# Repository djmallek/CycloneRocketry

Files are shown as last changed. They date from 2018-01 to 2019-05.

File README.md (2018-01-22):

# Cyclone Rocketry

This is an avionics control board for Iowa State's Cyclone Rocketry club. Our rocketry must carry a payload to a target altitude of 10,000ft.  Score is determined by how close a team's rocket can get to the target altitude, among other things.  To ensure we hit our target altitude, we have an air brakes system which actively calculates when and how long it needs to deploy it's air brakes system.  The board additionally provides data-logging and radio-relayed GPS tracking.

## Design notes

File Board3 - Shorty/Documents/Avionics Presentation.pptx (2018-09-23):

## Avionics Board

Danny

## What it do?

- Take environmental data (sensors)
- Log data
- Calculate when to move airbrakes
- Move airbrakes

## Sensors?

- IMU (gyro + accelerometer)
- Barometer (pressure sensor)
- Temperature
- GPS (location + super accurate time)
- Airbrake Position

## What else?

- 900MHz Radio for transmitting location
- Micro SD Card for datalogging
- Position monitoring of airbrakes
- Control of airbrakes using PWM (Pulse width modulation)
- Battery charging circuit (charges over USB)

## How to program?

- Through Arduino IDE! Super Easy!
- Go here: https://learn.adafruit.com/adafruit-feather-m0-basic-proto/setup and follow the instructions for “Arduino IDE Setup”, “Using with Arduino IDE”, and “Adapting Sketches to M0”

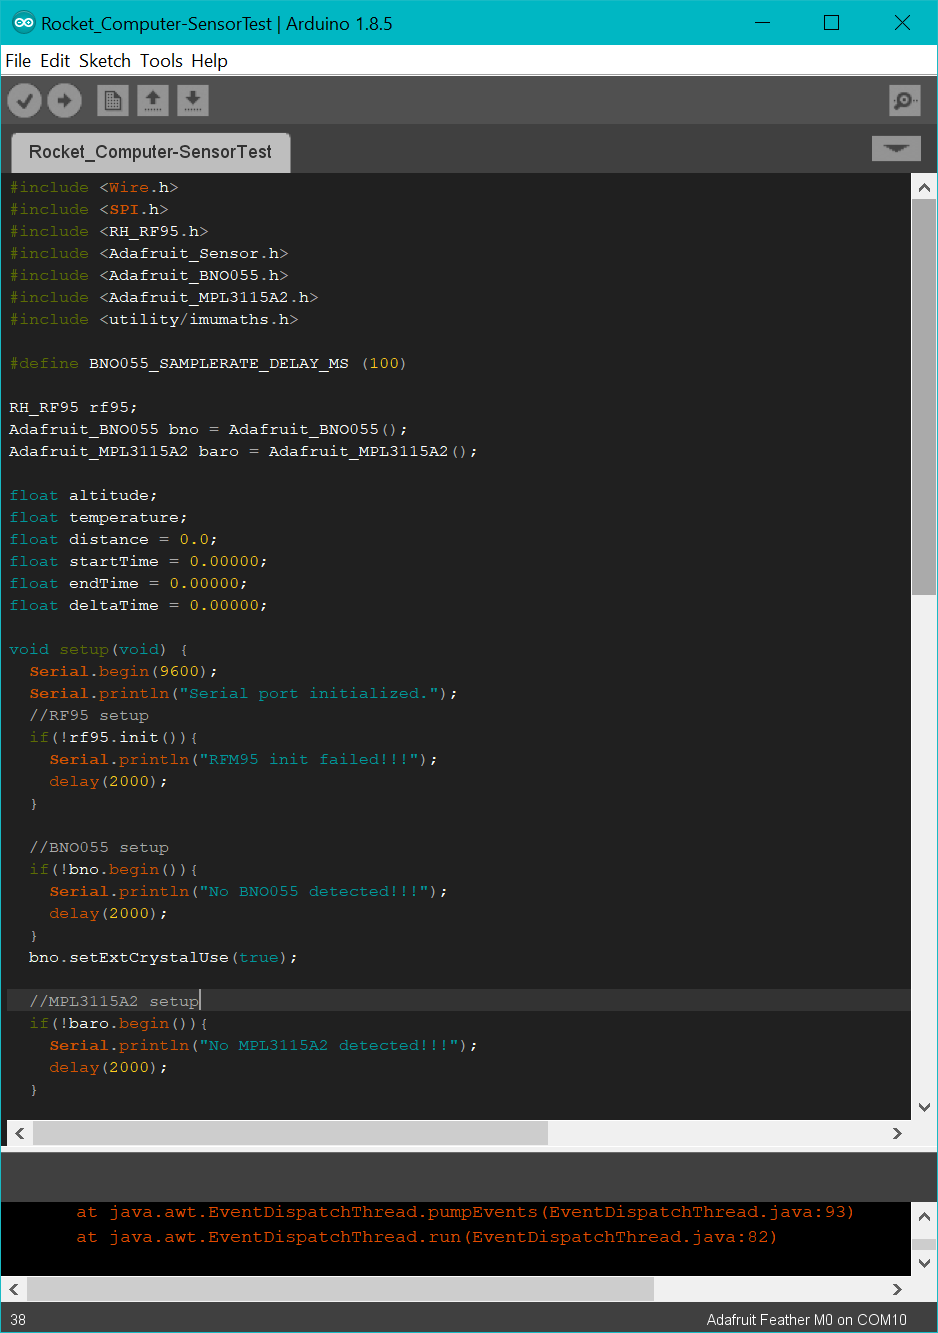
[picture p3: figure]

## Pictures

Manifest logo will change to Rocket Shop

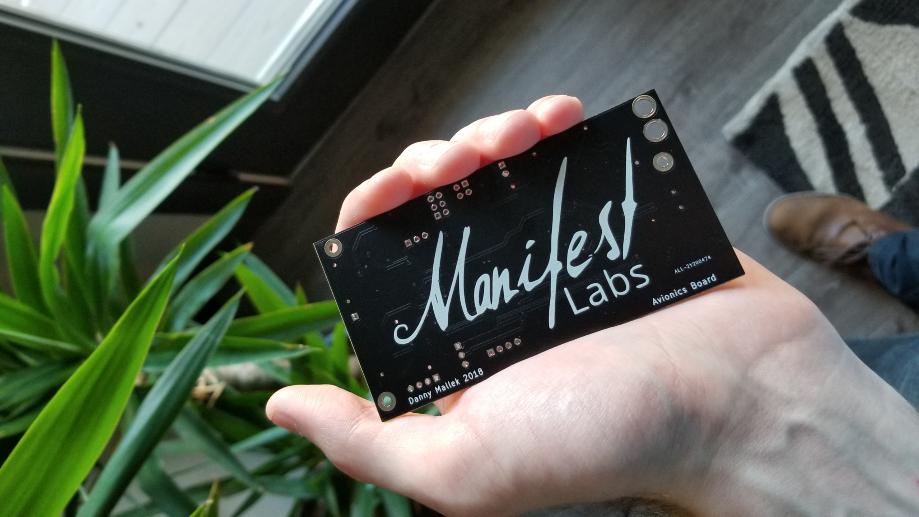
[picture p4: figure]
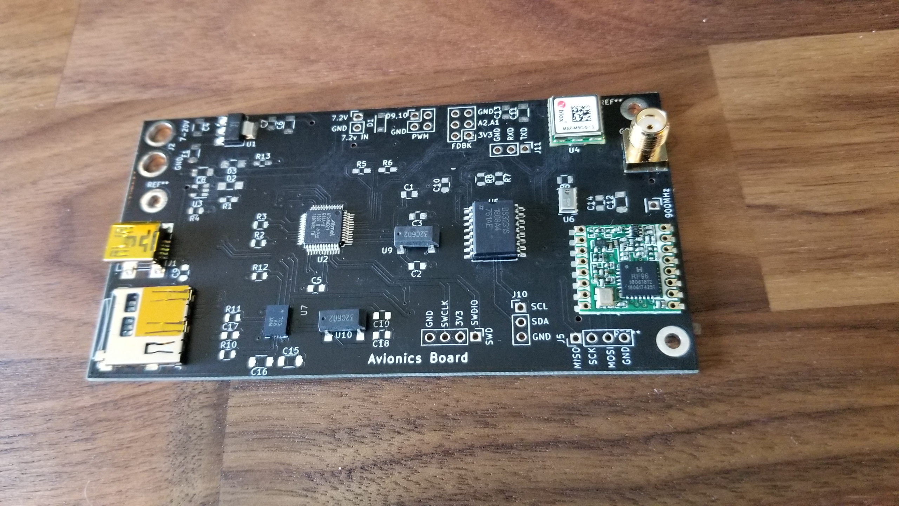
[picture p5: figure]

## Looking forward

- Avionics Board
  - Add status LEDs
  - Better power systems
  - Smaller board
  - Better connectors
  - More sensors? A second accelerometer for higher G’s?

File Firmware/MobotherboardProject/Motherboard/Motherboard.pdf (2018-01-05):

## Motherboard Project Configuration Report

# 1. Description

## 1.1. Project

Project Name | Motherboard
Board Name | Motherboard
Generated with: | STM32CubeMX 4.20.1
Date | 06/13/2017

## 1.2. MCU

MCU Series | STM32F4
MCU Line | STM32F411
MCU name | STM32F411RETx
MCU Package | LQFP64
MCU Pin number | 64

# 2. Pinout Configuration

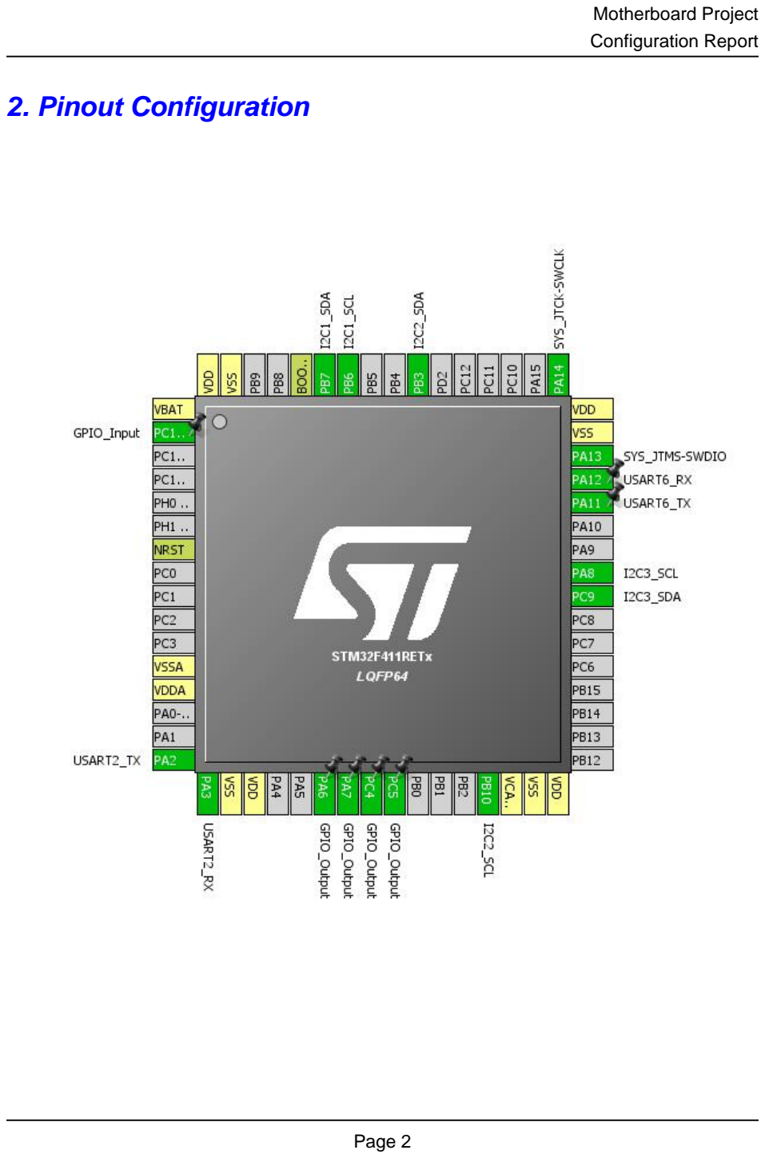
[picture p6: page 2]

# 3. Pins Configuration

Pin Number LQFP64 | Pin Name (function after reset) | Pin Type | Alternate Function(s) | Label
1 | VBAT | Power
2 | PC13-ANTI_TAMP * | I/O | GPIO_Input
7 | NRST | Reset
12 | VSSA | Power
13 | VDDA | Power
16 | PA2 | I/O | USART2_TX
17 | PA3 | I/O | USART2_RX
18 | VSS | Power
19 | VDD | Power
22 | PA6 * | I/O | GPIO_Output
23 | PA7 * | I/O | GPIO_Output
24 | PC4 * | I/O | GPIO_Output
25 | PC5 * | I/O | GPIO_Output
29 | PB10 | I/O | I2C2_SCL
30 | VCAP1 | Power
31 | VSS | Power
32 | VDD | Power
40 | PC9 | I/O | I2C3_SDA
41 | PA8 | I/O | I2C3_SCL
44 | PA11 | I/O | USART6_TX
45 | PA12 | I/O | USART6_RX
46 | PA13 | I/O | SYS_JTMS-SWDIO
47 | VSS | Power
48 | VDD | Power
49 | PA14 | I/O | SYS_JTCK-SWCLK
55 | PB3 | I/O | I2C2_SDA
58 | PB6 | I/O | I2C1_SCL
59 | PB7 | I/O | I2C1_SDA
60 | BOOT0 | Boot
63 | VSS | Power
64 | VDD | Power

## * The pin is affected with an I/O function

# 4. Clock Tree Configuration

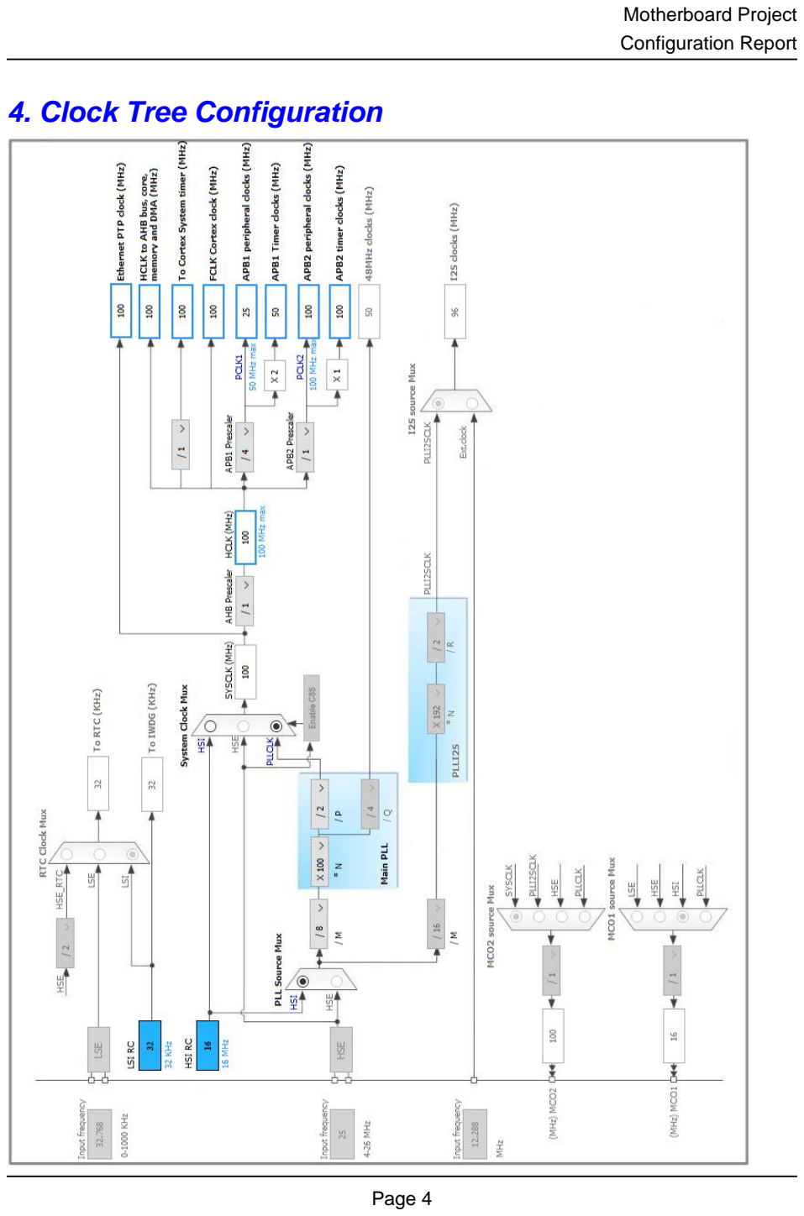
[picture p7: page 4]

# 5. IPs and Middleware Configuration

# 5.1. I2C1

## I2C: I2C

## 5.1.1. Parameter Settings:

### Master Features:

I2C Speed Mode | Standard Mode
I2C Clock Speed (Hz) | 100000

### Slave Features:

Clock No Stretch Mode | Disabled
Primary Address Length selection | 7-bit
Dual Address Acknowledged | Disabled
Primary slave address | 0
General Call address detection | Disabled

# 5.2. I2C2

## I2C: I2C

## 5.2.1. Parameter Settings:

### Master Features:

I2C Speed Mode | Standard Mode
I2C Clock Speed (Hz) | 100000

### Slave Features:

Clock No Stretch Mode | Disabled
Primary Address Length selection | 7-bit
Dual Address Acknowledged | Disabled
Primary slave address | 0
General Call address detection | Disabled

# 5.3. I2C3

## I2C: I2C

## 5.3.1. Parameter Settings:

### Master Features:

I2C Speed Mode | Standard Mode
I2C Clock Speed (Hz) | 100000

### Slave Features:

Clock No Stretch Mode | Disabled
Primary Address Length selection | 7-bit
Dual Address Acknowledged | Disabled
Primary slave address | 0
General Call address detection | Disabled

# 5.4. SYS

## Debug: Serial Wire Timebase Source: SysTick

# 5.5. USART2

## Mode: Asynchronous

## 5.5.1. Parameter Settings:

### Basic Parameters:

Baud Rate | 9600 *
Word Length | 8 Bits (including Parity)
Parity | None
Stop Bits | 1

### Advanced Parameters:

Data Direction | Receive and Transmit
Over Sampling | 16 Samples

# 5.6. USART6

## Mode: Asynchronous

## 5.6.1. Parameter Settings:

### Basic Parameters:

Baud Rate | 9600 *
Word Length | 8 Bits (including Parity)
Parity | None
Stop Bits | 1

### Advanced Parameters:

Data Direction | Receive and Transmit
Over Sampling | 16 Samples

### * User modified value

# 6. System Configuration

# 6.1. GPIO configuration

IP | Pin | Signal | GPIO mode | GPIO pull/up pull down | Max Speed | User Label
I2C1 | PB6 | I2C1_SCL | Alternate Function Open Drain | Pull-up | Very High *
| PB7 | I2C1_SDA | Alternate Function Open Drain | Pull-up | Very High *
I2C2 | PB10 | I2C2_SCL | Alternate Function Open Drain | Pull-up | Very High *
| PB3 | I2C2_SDA | Alternate Function Open Drain | Pull-up | Very High *
I2C3 | PC9 | I2C3_SDA | Alternate Function Open Drain | Pull-up | Very High *
| PA8 | I2C3_SCL | Alternate Function Open Drain | Pull-up | Very High *
SYS | PA13 | SYS_JTMS-SWDIO | n/a | n/a | n/a
| PA14 | SYS_JTCK-SWCLK | n/a | n/a | n/a
USART2 | PA2 | USART2_TX | Alternate Function Push Pull | Pull-up | Very High *
| PA3 | USART2_RX | Alternate Function Push Pull | Pull-up | Very High *
USART6 | PA11 | USART6_TX | Alternate Function Push Pull | Pull-up | Very High *
| PA12 | USART6_RX | Alternate Function Push Pull | Pull-up | Very High *
GPIO | PC13-ANTI_TAMP | GPIO_Input | Input mode | Pull-down * | n/a
| PA6 | GPIO_Output | Output Push Pull | No pull-up and no pull-down | Low
| PA7 | GPIO_Output | Output Push Pull | No pull-up and no pull-down | Low
| PC4 | GPIO_Output | Output Push Pull | No pull-up and no pull-down | Low
| PC5 | GPIO_Output | Output Push Pull | No pull-up and no pull-down | Low

# 6.2. DMA configuration

## nothing configured in DMA service

# 6.3. NVIC configuration

Interrupt Table | Enable | Preenmption Priority | SubPriority
Non maskable interrupt | true | 0 | 0
Hard fault interrupt | true | 0 | 0
Memory management fault | true | 0 | 0
Pre-fetch fault, memory access fault | true | 0 | 0
Undefined instruction or illegal state | true | 0 | 0
System service call via SWI instruction | true | 0 | 0
Debug monitor | true | 0 | 0
Pendable request for system service | true | 0 | 0
System tick timer | true | 0 | 0
PVD interrupt through EXTI line 16 | unused
Flash global interrupt | unused
RCC global interrupt | unused
I2C1 event interrupt | unused
I2C1 error interrupt | unused
I2C2 event interrupt | unused
I2C2 error interrupt | unused
USART2 global interrupt | unused
USART6 global interrupt | unused
I2C3 event interrupt | unused
I2C3 error interrupt | unused
FPU global interrupt | unused

### * User modified value

# 7. Power Consumption Calculator report

### 7.1. Microcontroller Selection

Series | STM32F4
Line | STM32F411
MCU | STM32F411RETx
Datasheet | 026289_Rev4

### 7.2. Parameter Selection

Temperature | 25
Vdd | null

# 8. Software Project

## 8.1. Project Settings

Name | Value
Project Name | Motherboard
Project Folder | C:\Users\djmal\Documents\GitHub\FoxWestern\Firmware\MobotherboardProject\
Toolchain / IDE | SW4STM32
Firmware Package Name and Version | STM32Cube FW_F4 V1.16.0

## 8.2. Code Generation Settings

Name | Value
STM32Cube Firmware Library Package | Copy only the necessary library files
Generate peripheral initialization as a pair of '.c/.h' files | No
Backup previously generated files when re-generating | No
Delete previously generated files when not re-generated | Yes
Set all free pins as analog (to optimize the power consumption) | No

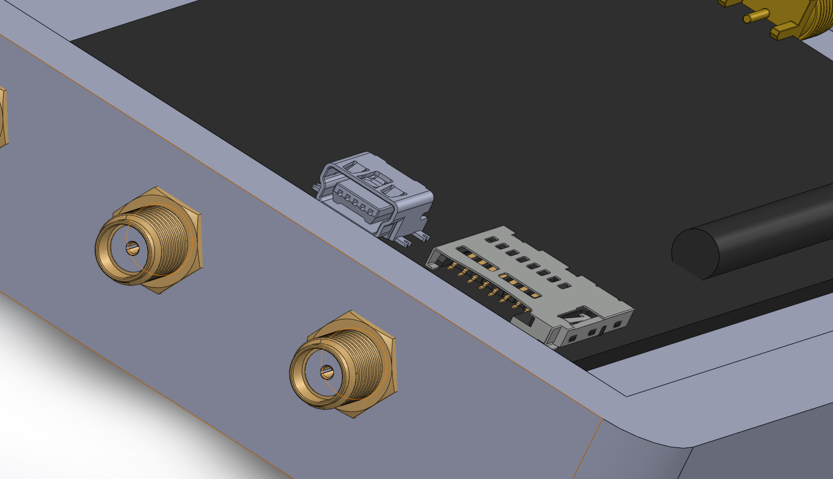
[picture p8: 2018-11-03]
Board3 - Shorty/Documents/Avionics Chassis/Screenshots/shot6.PNG

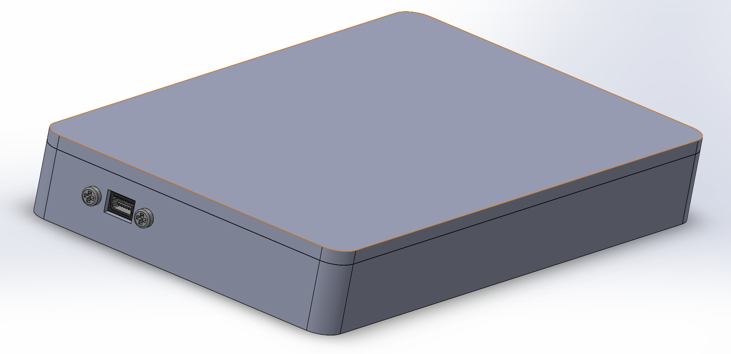
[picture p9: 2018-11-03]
Board3 - Shorty/Documents/Avionics Chassis/Screenshots/shot1.PNG

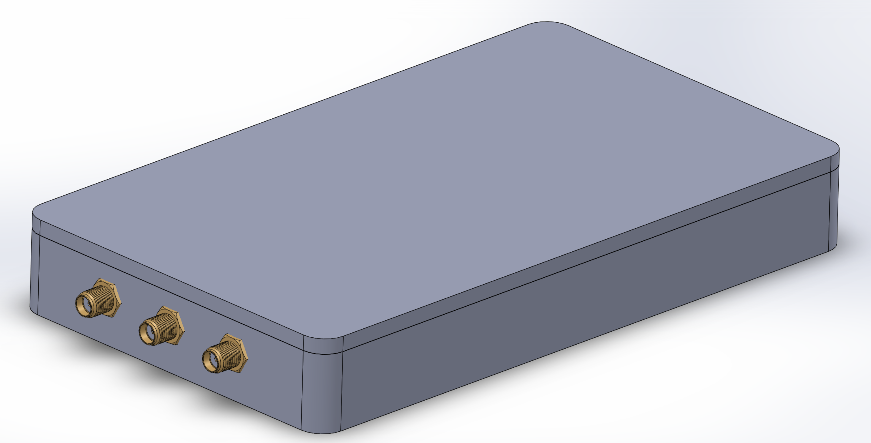
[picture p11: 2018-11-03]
Board3 - Shorty/Documents/Avionics Chassis/Screenshots/shot2.PNG

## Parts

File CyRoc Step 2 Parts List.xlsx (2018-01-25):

Part Name | Vendor | Part Number | Price Each | Qty | Total Price | Description
2.54mm Male Header (https://www.amazon.com/Hotop-Pack-Single-Header-Connector/dp/B06XR8CV8P) | Amazon | B06XR8CV8P | $6.99 | 1 | $6.99
2.54mm Female Header (https://www.amazon.com/2-54mm-Straight-Single-Female-Headers/dp/B00899WQ6U) | Amazon | B00899WQ6U | $4.63 | 1 | $4.63
Female XT60 (https://www.amazon.com/Finware-Female-Bullet-Connectors-Battery/dp/B01ETROGP4) | Amazon | B01ETROGP4 | $8.45 | 1 | $8.45
2.54mm Female Angle Header (2x8) (https://www.digikey.com/product-detail/en/sullins-connector-solutions/PPPC082LJBN-RC/S5561-ND/776019) | Digikey | S5561-ND | $1.38 | 2 | $2.76
10uF 0805 Cap (https://www.digikey.com/product-detail/en/murata-electronics-north-america/GRM219R60J106KE19D/490-3340-1-ND/702881) | Digikey | 490-3340-1-ND | $0.10 | 10 | $1.05
0805 LED Green (https://www.digikey.com/product-detail/en/lite-on-inc/LTST-C171KGKT/160-1426-1-ND/386798) | Digikey | 160-1426-1-ND | $0.31 | 3 | $0.93
0805 LED Red (https://www.digikey.com/product-detail/en/lite-on-inc/LTST-C171KRKT/160-1427-1-ND/386800) | Digikey | 160-1427-1-ND | $0.31 | 6 | $1.86
220 ohm 0805 Res (https://www.digikey.com/product-detail/en/rohm-semiconductor/ESR10EZPJ221/RHM220KCT-ND/1762990) | Digikey | RHM220KCT-ND | $0.09 | 10 | $0.87
2.2 kohm 0805 Res (https://www.digikey.com/product-detail/en/rohm-semiconductor/ESR10EZPJ222/RHM2.2KKCT-ND/1762991) | Digikey | RHM2.2KKCT-ND | $0.09 | 10 | $0.87
TL1963 (https://www.digikey.com/product-detail/en/texas-instruments/TL1963A-33DCYR/296-24897-1-ND/2118661) | Digikey | 296-24897-1-ND | $2.94 | 2 | $5.88 | Part was cheap when originally designed, but not now. Not changing for $1 savings. Will Change in step 3
LM340MP-5.0 (https://www.digikey.com/product-detail/en/texas-instruments/LM340MP-5.0-NOPB/LM340MP-5.0-NOPBCT-ND/270747) | Digikey | LM340MP-5.0/NOPBCT-ND | $1.36 | 2 | $2.72 | RFD900 consumes 1A at peak consumption. Consider a larger currentchip for step 3 if it is a problem here.
Adafruit Datalogger (https://www.adafruit.com/product/254) | Adafruit | 254 | $7.50 | 1 | $7.50
Adafruit DS3231 (https://www.adafruit.com/product/3013) | Adafruit | 3013 | $13.95 | 1 | $13.95
Adaruit MCP9808 (https://www.adafruit.com/product/1782) | Adafruit | 1782 | $4.95 | 1 | $4.95
Adafruit ADXL377 (https://www.adafruit.com/product/1413) | Adafruit | 1413 | $24.95 | 1 | $24.95
Adafruit BNO055 (https://www.adafruit.com/product/2472) | Adafruit | 2472 | $34.95 | 1 | $34.95
Adafruit MPL115A2 (https://www.adafruit.com/product/992) | Adafruit | 992 | $7.95 | 1 | $7.95
Adafruit GPS (https://www.adafruit.com/product/746) | Adafruit | 746 | $39.95 | 1 | $39.95
Adafruit GPS Antenna (https://www.adafruit.com/product/960) | Adafruit | 960 | $12.95 | 1 | $12.95 | KEEP AWAY FROM OTHER SENSORS!! ESP THE MAGNETOMETER. THE MAGNET WILL MESS IT UP!
Adafruit GPS Antenna Adapter (https://www.adafruit.com/product/851) | Adafruit | 851 | $3.95 | 1 | $3.95
3S 2200 mAh Lithium Battery (https://hobbyking.com/en_us/turnigy-2200mah-3s-25c-lipo-pack.html?___store=en_us) | Hobby King | T2200.3S.25 | $10.99 | 2 | $21.98 | Optional, but I recommend buying at least 1. This is so we can test it while it's not hooked up to the computer.
Aluminum, 7/32", hex, 2-56, standoff | McMaster | 93505A513 | $0.78 | 30 | $23.40 | Aluminum because steel is expensive and magnetic. I know you're supposed to match materials.
Stainless steel, hex, 2-56, 3/16" screw (100 pk.) | McMaster | 92949A076 | $5.42 | 1 | $5.42 | Steel because alternatives suck
Stainless steel, hex, 2-56, nut (100 pk.) | McMaster | 91841A003 | $3.03 | 1 | $3.03 | See above
RFD900+ (http://store.rfdesign.com.au/rfd-900p-modem/) | RFDesign Ltd. | MODEM-RFD900+ | $77.71 | 2 | $155.42 | $AUD 99.50 = $USD 77.71. Ships from Australia. These radios allow communication between the rocket and the base station.
 |  |  |  |  | $397.36 | **Does not include shipping
 |  |  |  |  |  | ***RFD900s, GPS, GPS Antenna, GPS antenna adapters, can be reused in Step 3. We already bought a lot of the sensors and them can be pulled from the breadboard.

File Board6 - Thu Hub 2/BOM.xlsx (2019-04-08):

Part | Qty | Price Each | Price Total | Description
Feather M0 Datalogger (https://www.digikey.com/products/en/development-boards-kits-programmers/evaluation-and-demonstration-boards-and-kits/787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) | 1 | $19.95 | $19.95
RFM95 Breakout (https://www.digikey.com/product-detail/en/adafruit-industries-llc/3072/1528-1667-ND/6005357) | 1 | $19.95 | $19.95
BNO055 Breakout (https://www.adafruit.com/product/2472) | 1 | $34.95 | $34.95
XT60 Female | 1 |  | $0.00
AZ1117-3.3 (https://www.digikey.com/short/pjd2mb) | 2 | $0.44 | $0.88
L7806ABD2T-TR (https://www.digikey.com/short/pjd2mv) | 2 | $0.85 | $1.70
GT-U7 GPS (https://www.amazon.co.uk/MakerHawk-Microcontroller-Compatible-Navigation-Positioning/dp/B0783H7BLW?s=gateway) | 1 | $9.95 | $9.95
MPL3115A2 Breakout (https://www.adafruit.com/product/1893) | 1 | $9.95 | $9.95
Buzzer (https://www.digikey.com/short/pjd2bw) | 1 | $3.52 | $3.52
0805 2.2K Resistor (https://www.digikey.com/product-detail/en/yageo/RC0805FR-072K2L/311-2.20KCRCT-ND/730623) | 10 | $0.04 | $0.43
0805 220 Resistor (https://www.digikey.com/product-detail/en/te-connectivity-passive-product/CRGCQ0805F220R/A129741CT-ND/8577573) | 10 | $0.05 | $0.51
0805 330 Resistor (https://www.digikey.com/product-detail/en/te-connectivity-passive-product/CRG0805F330R/A106061CT-ND/3477707) | 10 | $0.05 | $0.52
0805 LED GREEN (https://www.digikey.com/product-detail/en/lite-on-inc/LTST-C171GKT/160-1423-1-ND/386792) | 4 | $0.29 | $1.16
0805 10u Cap (https://www.digikey.com/product-detail/en/samsung-electro-mechanics/CL21A106KPFNNNG/1276-6456-1-ND/5958084) | 10 | $0.10 | $1.00
PCB from AllPCB | 5 | $4.60 | $23.00
 |  | Total | $127.47

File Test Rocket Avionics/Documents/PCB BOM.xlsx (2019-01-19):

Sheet: Sheet1
 |  |  | xxxx xxxx xxxxx xxPCS BOM (Sample Bill of Materials)
Item # | *Ref Des | *Qty | Manufacturer | *Mfg Part # | Description / Value | *Package | Type | Your Instructions / Notes | Price |  | Cost Option Number | Cost | Description
1 | BT1 | 1 | Panasonic - BSG | BR-1225A/HBN (https://www.digikey.com/short/p7371j) | BATTERY LITHIUM 3V COIN 12.5MM | BR-1225A | DNP |  | $2.01 |  | 1 | $595.85 | Everything Installed on every board
2 | BZ1 | 1 | CUI | CMT-5023S-SMT-TR (https://www.digikey.com/short/p7371z) | SMD Piezio Buzzer | 3 POS SMD | DNP |  | $3.52 |  | 2 | $240.69 | All passives installed on every board, manually all other components installed on just one board
3 | C1,C5,C7,C9,C10,C13 | 7 | Samsung | CL21B105KAFNNNE (https://www.digikey.com/short/p7379m) | CAP CER 1UF 25V X7R 0805 | 805 | SMD |  | $0.77 |  | 3 | $156.75 | All passives installed on every board, nothing else installed
4 | C2,C3,C18,C19 | 4 | Samsung | CL21C220JB61PNC (https://www.digikey.com/short/p73790) | CAP CER 22PF 50V C0G,NP0 0805 | 805 | SMD |  | $0.84 |  | 4 | $270.76 | All passives and microcontrollers and sensors installed. LoRa and GPS components installed on one
5 | C4,C6,C11,C12,C20,C21 | 5 | Samsung | CL31B106MOHNNNE (https://www.digikey.com/short/p737r7) | CAP CER 10UF 16V X7R 1206 | 1206 | SMD |  | $1.30 |  | 5 | $135.37 | Manually install everything ourselves on just one board
6 | C8 | 1 | Yageo | CC0805KRX7R9BB103 (https://www.digikey.com/short/p737fc) | CAP CER 10000PF 50V X7R 0805 | 0805 | SMD |  | $0.11 |  | 6 | $159.05 | Danny's Option
7 | C15 | 1 | Yageo | CC0805KRX7R9BB682 (https://www.digikey.com/short/p737fn) | CAP CER 6800PF 50V X7R 0805 | 0805 | SMD |  | $0.13
8 | C16 | 1 | AVX Corperation | 08053C124KAT2A (https://www.digikey.com/short/p7372b) | CAP CER 0.12UF 25V X7R 0805 | 0805 | SMD |  | $0.36
9 | C14,C17 | 2 | Samsung | CL21B104MBCNNNC (https://www.digikey.com/short/p737wh) | CAP CER 0.1UF 50V X7R 0805 | 0805 | SMD |  | $0.20
10 | D1 | 1 | ON Semiconductor | MBR120ESFT1G (https://www.digikey.com/short/p737n9) | DIODE SCHOTTKY 20V 1A SOD123L | SOD-123L | SMD |  | $0.44
11 | D3,D4,D5,D6 | 4 | Stanley Electric Co | PG1101W-TR (https://www.digikey.com/short/p737dv) | LED GREEN CLEAR 3216 SMD | 1206 | SMD |  | $1.96
12 | J1 | 1 | EDAC Inc | 690-005-299-043 (https://www.digikey.com/short/p7370h) | CONN RCPT USB2.0 MINI B SMD R/A | 8 POS SMD | SMD |  | $0.65
13 | J2 | 1 | -- | -- | XT 60 Connector | 2 POS TH | DNP
14 | J3 | 1 | -- | -- | 2.54mm Pitch Male Header 1x4 | 4 POS TH | DNP
15 | J4 | 1 | -- | -- | 2.54mm Pitch Male Header 1x2 | 2 POS TH | DNP
16 | J5 | 1 | -- | -- | 2.54mm Pitch Male Header 1x4 | 4 POS TH | DNP
17 | J6 | 1 | Wurth Electronics Inc. | 693072010801 (https://www.digikey.com/short/p73tqd) | CONN MICRO SD CARD HINGED TYPE | 12 POS SMD | DNP |  | $3.20
18 | J7,J12 | 2 | Molex, LLC | 733910070 (https://www.digikey.com/short/p73t84) | CONN SMA RCPT STR 50 OHM PCB | 5 POS TH | DNP |  | $5.68
19 | J8 | 1 | -- | -- | 2.54mm Pitch Male Header 2x3 | 6 POS TH | DNP
20 | J9 | 1 | -- | -- | 2.54mm Pitch Male Header 2x2 | 4 POS TH | DNP
21 | J10 | 1 | -- | -- | 2.54mm Pitch Male Header 1x3 | 3 POS TH | DNP
22 | J11 | 1 | -- | -- | 2.54mm Pitch Male Header 1x3 | 3 POS TH | DNP
23 | J13,J14 | 2 | -- | -- | 2.54mm Pitch Male Header 1x1 | 1 POS TH | DNP
24 | R1 | 1 | Stackpole Electronics Inc. | RNCP0805FTD10R0 (https://www.digikey.com/short/p73tpf) | RES 10 OHM 1% 1/4W 0805 | 0805 | SMD |  | $0.10
25 | R2,R3 | 2 | Yageo | RC0805FR-072K2L (https://www.digikey.com/short/p73tp1) | RES SMD 2.2K OHM 1% 1/8W 0805 | 0805 | SMD |  | $0.20
26 | R4 | 1 | Stackpole Electronics Inc. | RMCF0805JT330R (https://www.digikey.com/short/p73tzj) | RES 330 OHM 5% 1/8W 0805 | 0805 | SMD |  | $0.10
27 | R7,R8,R10,R11,R12 | 5 | Stackpole Electronics Inc. | RMCF0805FT10K0 (https://www.digikey.com/short/p73t43) | RES 10K OHM 1% 1/8W 0805 | 0805 | SMD |  | $0.50
28 | R13,R19,R20,R21 | 4 | Yageo | RC0805FR-071KL (https://www.digikey.com/short/p73t42) | RES SMD 1K OHM 1% 1/8W 0805 | 0805 | SMD |  | $0.40
29 | U1 | 1 | Linear Technology | LT1117CST-3.3#TRPBF (https://www.digikey.com/short/p733vw) | IC REG LIN 3.3V 800MA SOT223-3 | SOT-223-3 | DNP |  | $4.59
30 | U2 | 1 | Microchip Technology | ATSAMD21G18A-AUT (https://www.digikey.com/short/p73318) | IC MCU 32BIT 256KB FLASH 48TQFP | 48-TQFP (7x7) | SMD |  | $3.22
31 | U3 | 1 | Microchip Technology | MCP1825ST-3302E/DB (https://www.digikey.com/short/p73qc3) | IC REG LIN 3.3V 500MA SOT223-3 | SOT-223-3 | SMD |  | $0.53
32 | U4 | 1 | U-Blox America Inc. | MAX-M8W-0 (https://www.digikey.com/short/p73qc5) | IC RECEIVER GPS/GNSS 18LCC | 18 POS SMD | DNP |  | $27.00 | $18 after qty 10
33 | U5 | 1 | Maxim Integrated | DS3231S#T&R (https://www.digikey.com/short/p73q73) | IC RTC CLK/CALENDAR I2C 16-SOIC | 16-SOIC | DNP |  | $8.68
34 | U6 | 1 | NXP USA Inc. | MPL3115A2 (https://www.digikey.com/short/p73q7r) | IC ALTIMETER I2C VERSION 8LGA | 8-LGA (3x5) | DNP |  | $5.80
35 | U7 | 1 | Bosch Sensortec | BNO055 (https://www.digikey.com/short/p73q71) | IMU ACCEL/GYRO/MAG I2C 28LGA | 28-LGA (5.2x3.8) | DNP |  | $12.07
36 | U8 | 1 | RF Solutions | RFM95W-915S2 (https://www.digikey.com/short/p73qtb) | LORA TRX MODULE +20DBM/-139DBM 3 | 16 POS SMD | DNP |  | $14.81
37 | U9 | 2 | ECS Inc. | ECS-.327-12.5-17X-TR (https://www.digikey.com/short/p73q3c) | CRYSTAL 32.7680KHZ 12.5PF SMD | 4-SOJ 5.50mm pitch | SMD |  | $1.20
 |  |  |  |  |  |  |  |  | $100.37
 |  | 50
 | DNP= Do not populate
 | * Must filled |  |  |  |  |  |  | Cost of PCB | 17
 |  |  |  |  |  |  |  | 0

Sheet: Power
Name | Max Power
GPS | 72 | mA
MCU | 50 | mA
LoRa | 130 | Ma
 | 252

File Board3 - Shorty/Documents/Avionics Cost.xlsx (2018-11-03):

Part | qty | cost | total | description
Button Head Hex Screw 4-40, 1/2" Long (100pk.) (https://www.mcmaster.com/92949a110) | 1 | $3.38 | $3.38 | Attaching Size 14 circular connector
Flat Head Hex Screw 4-40, 1/2" Long (100pk.) (https://www.mcmaster.com/92210a110) | 1 | $3.68 | $3.68 | Attaching top and bottom plates
12 Position Female Receptacle RT001412SNH-K (https://www.digikey.com/short/j0bjq0) | 1 | $20.31 | $20.31 | Power out, PWM, feedback, and I2C out
12 Position Male Plug Connector RT061412PNH-K (https://www.digikey.com/short/j0bj8f) | 1 | $28.90 | $28.90 | Plug for wire harness
4-40 Hex Nut (100pk.) (https://www.mcmaster.com/91831a005) | 1 | $3.90 | $3.90 | Hex nut
2"x4"x6" 6061 Aluminum Billet (https://www.ebay.com/itm/2-X-4-X-6-6061-aluminum-new-stock-cnc-machining-tool-solid-block-machineable-/323435057633) | 1 | $27.99 | $27.99 | For machinig avionics chassis
 |  |  | $88.16

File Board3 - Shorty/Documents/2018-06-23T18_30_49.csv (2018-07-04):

Index | Quantity | Part Number | Description | Customer Reference | Available Quantity | Backorder Quantity | Unit Price USD | Extended Price USD
1 | 1 | 36-1058-ND | COIN CELL HLDR 20MM 2025/2032 |  | 0 | 1 | 1.79000 | 1.79
2 | 10 | 490-1691-1-ND | CAP CER 1UF 16V X7R 0805 |  | 10 | 0 | 0.14300 | 1.43
3 | 10 | 1276-2720-1-ND | CAP CER 10UF 25V X5R 1206 |  | 10 | 0 | 0.19800 | 1.98
4 | 4 | XC1195CT-ND | CRYSTAL 32.7680KHZ 12.5PF SMD |  | 4 | 0 | 0.56000 | 2.24
5 | 10 | 1276-1120-1-ND | CAP CER 12PF 50V C0G/NP0 0805 |  | 10 | 0 | 0.05500 | 0.55
6 | 2 | 399-16723-1-ND | CAP CER 1206 6.8NF 1000V X7R 10% |  | 2 | 0 | 0.40000 | 0.80
7 | 2 | BZT52C15-FDICT-ND | DIODE ZENER 15V 500MW SOD123 |  | 2 | 0 | 0.24000 | 0.48
8 | 3 | 160-1456-1-ND | LED GREEN CLEAR 1206 SMD |  | 3 | 0 | 0.34000 | 1.02
9 | 5 | 507-1805-1-ND | PTC RESET FUSE 16V 750MA 1206 |  | 5 | 0 | 0.20000 | 1.00
10 | 10 | RR08P1.0KDCT-ND | RES SMD 1K OHM 0.5% 1/16W 0603 |  | 10 | 0 | 0.09800 | 0.98
11 | 10 | 311-2.20KCRCT-ND | RES SMD 2.2K OHM 1% 1/8W 0805 |  | 10 | 0 | 0.02200 | 0.22
12 | 10 | RR08P100KDCT-ND | RES SMD 100K OHM 0.5% 1/16W 0603 |  | 10 | 0 | 0.09800 | 0.98
13 | 10 | RR12P10.0KDCT-ND | RES SMD 10K OHM 0.5% 1/10W 0805 |  | 10 | 0 | 0.09800 | 0.98
14 | 1 | RFM95W-915S2-ND | LORA TRX MODULE +20DBM/-139DBM 3 |  | 1 | 0 | 14.11000 | 14.11
15 | 1 | 672-1002-1-ND | IC RECEIVER GPS/GNSS 18LCC |  | 1 | 0 | 23.50000 | 23.50
16 | 2 | 151-1206-1-ND | CONN MINI USB RCPT RA TYPE B SMD |  | 2 | 0 | 0.54000 | 1.08
17 | 1 | 732-3819-1-ND | CONN MICRO SD CARD PUSH-PUSH R/A |  | 1 | 0 | 2.92000 | 2.92
18 | 1 | CONSMA001-SMD-G-ND | CONN SMA RCPT STR 50 OHM SMD |  | 1 | 0 | 2.86000 | 2.86
19 | 1 | 296-24897-1-ND | IC REG LINEAR 3.3V 1.5A SOT223-4 |  | 1 | 0 | 2.94000 | 2.94
20 | 2 | ATSAMD21G18A-AU-ND | IC MCU 32BIT 256KB FLASH 48TQFP |  | 2 | 0 | 3.15000 | 6.30
21 | 2 | MCP73831T-2ACI/OTCT-ND | IC CONTROLLR LI-ION 4.2V SOT23-5 |  | 2 | 0 | 0.58000 | 1.16
22 | 1 | DS3231S#T&RCT-ND | IC RTC CLK/CALENDAR I2C 16-SOIC |  | 1 | 0 | 8.68000 | 8.68
23 | 1 | MPL115A2-ND | IC BAROMETER I2C DGTL MINI 8LGA |  | 1 | 0 | 6.70000 | 6.70
24 | 1 | 828-1058-1-ND | IMU ACCEL/GYRO/MAG I2C 28LGA |  | 1 | 0 | 12.07000 | 12.07

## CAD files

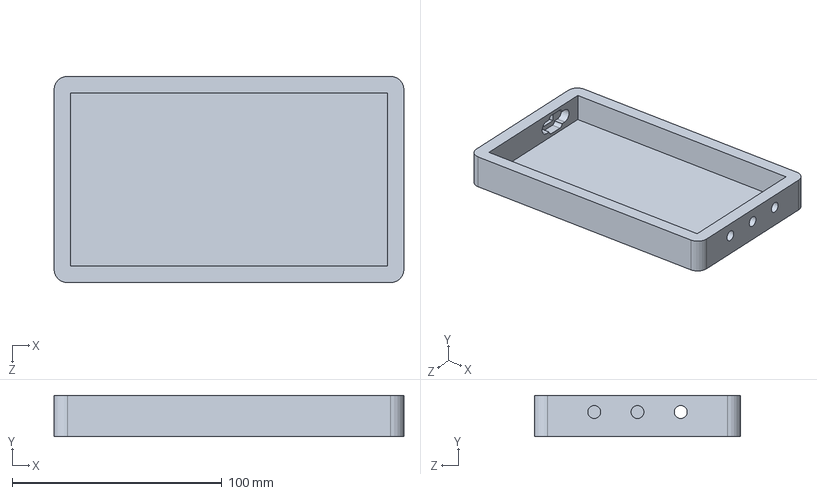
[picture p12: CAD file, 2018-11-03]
Board3 - Shorty/Documents/Avionics Chassis/Main plate.SLDPRT
167.0 x 19.7 x 98.4 mm

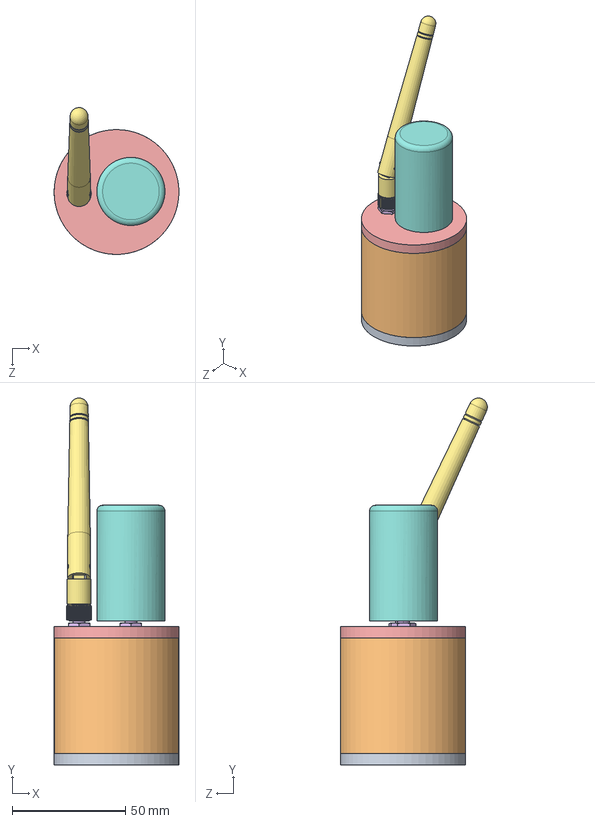
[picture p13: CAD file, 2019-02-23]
Test Rocket Avionics/Solidworks Models/EBay.SLDASM
55.0 x 161.7 x 64.7 mm
EBay Endcap
Nose Cone Coupler
5mm Standoff x 8
Avionics PCB x 2
EBay Endcap Antennas
SMA x 2
915MHz Antenna
M1227HCT-A2-SMA

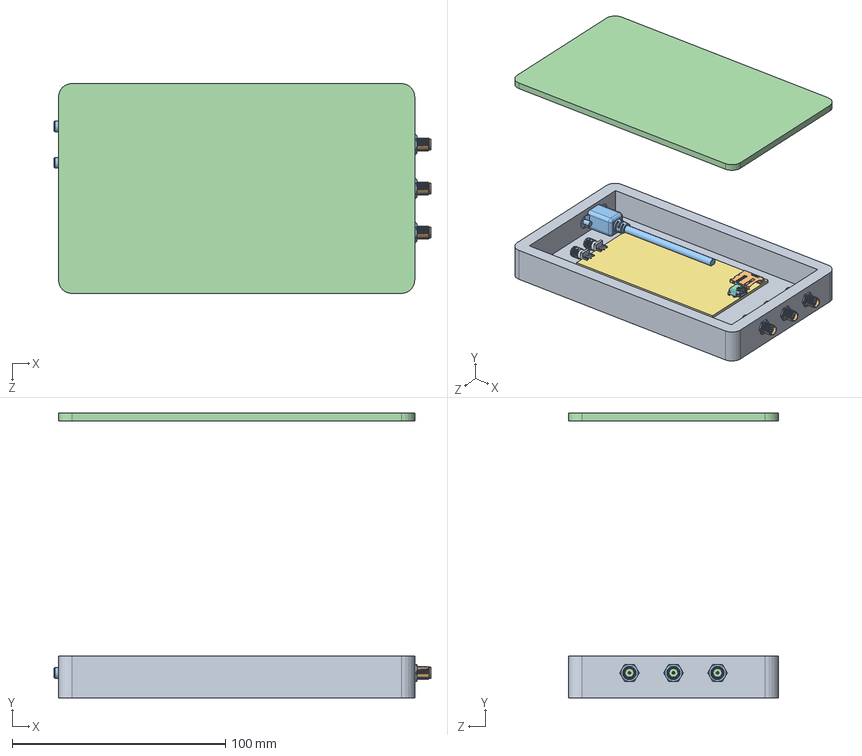
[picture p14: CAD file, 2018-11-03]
Board3 - Shorty/Documents/Avionics Chassis/AvionicsCase.SLDASM
176.7 x 133.5 x 98.4 mm
Main plate
BD11ACS01A x 3
HN8-1X4-36X16 x 3
SMA7471B1-2T-50 x 3
SMA7471B1-2T-50_1 x 3
SMA7910-3 x 3
AvionicBoard
USB_Mini_B_SMD_buchse
SMA CONNECTOR - EMPCB.SMAFSTJ.B.HT x 2
microSD
TopPlate

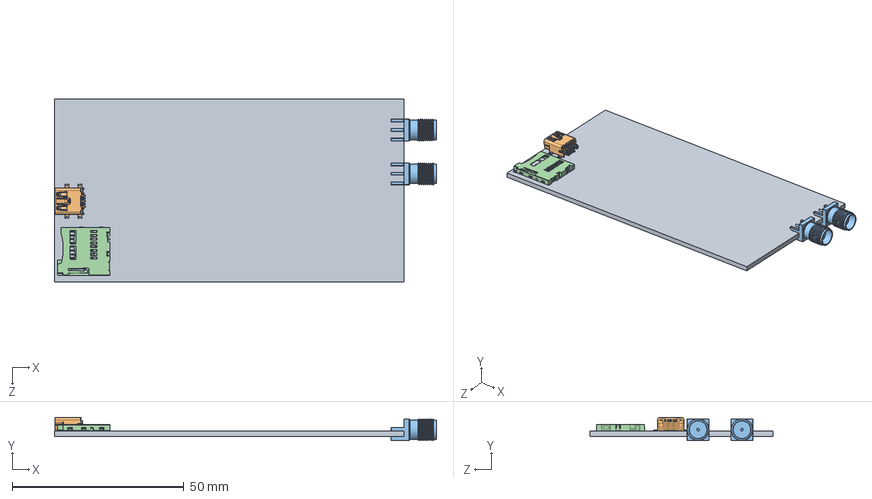
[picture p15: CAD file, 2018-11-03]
Board3 - Shorty/Documents/Avionics Chassis/Avionics.SLDASM
111.1 x 6.76 x 53.3 mm
AvionicBoard
USB_Mini_B_SMD_buchse
SMA CONNECTOR - EMPCB.SMAFSTJ.B.HT x 2
microSD

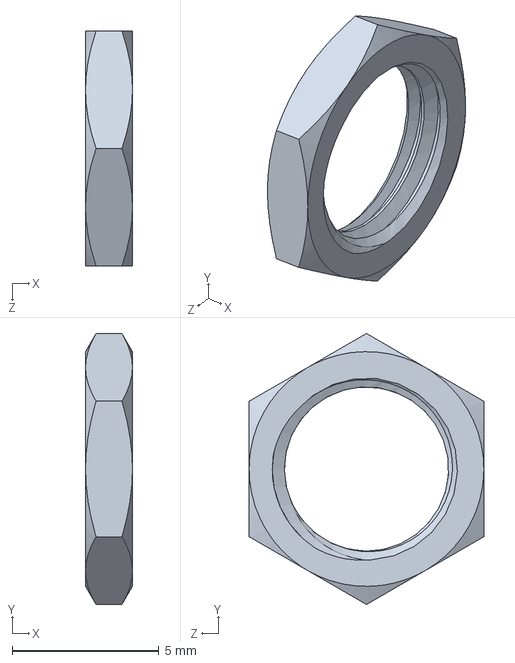
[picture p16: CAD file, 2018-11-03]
Board3 - Shorty/Documents/Avionics Chassis/132170/HN8-1X4-36X16.sldprt
1.60 x 9.24 x 8.00 mm

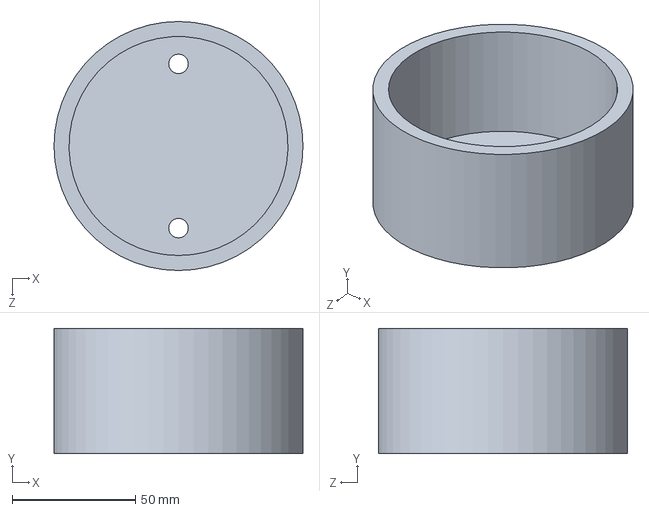
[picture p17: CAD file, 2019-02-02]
Board5 - Circular Feather/Base Chassis.SLDPRT
101.1 x 50.8 x 101.1 mm

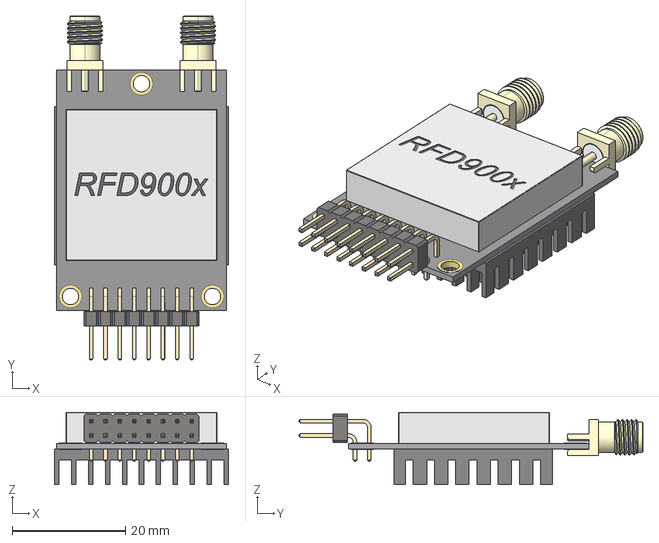
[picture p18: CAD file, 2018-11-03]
kicad libraries/3D Models/RFD900X.stp
30.8 x 60.8 x 12.8 mm

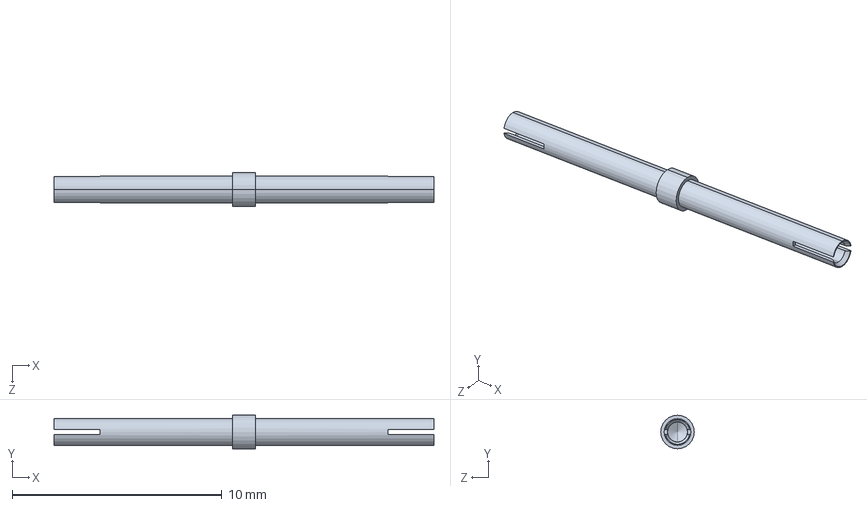
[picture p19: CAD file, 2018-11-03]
Board3 - Shorty/Documents/Avionics Chassis/132170/SMA7910-3.sldprt
18.1 x 1.60 x 1.60 mm

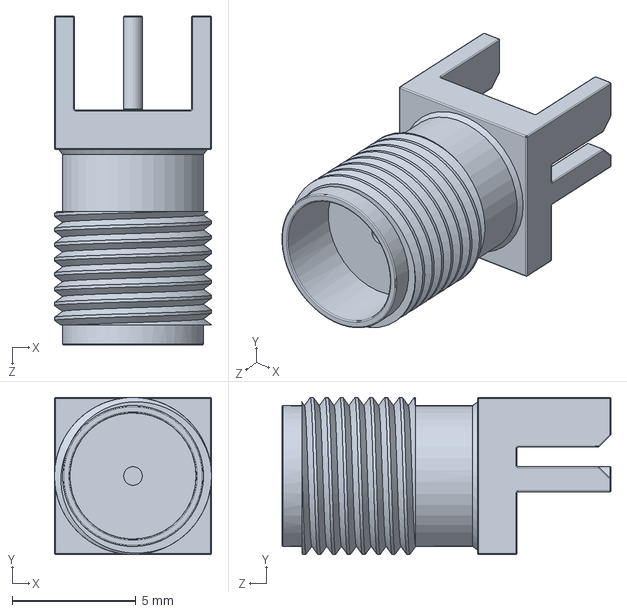
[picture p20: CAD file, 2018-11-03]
Board3 - Shorty/Documents/Avionics Chassis/SMA CONNECTOR - EMPCB.SMAFSTJ.B.HT.SLDPRT
6.35 x 6.35 x 13.3 mm

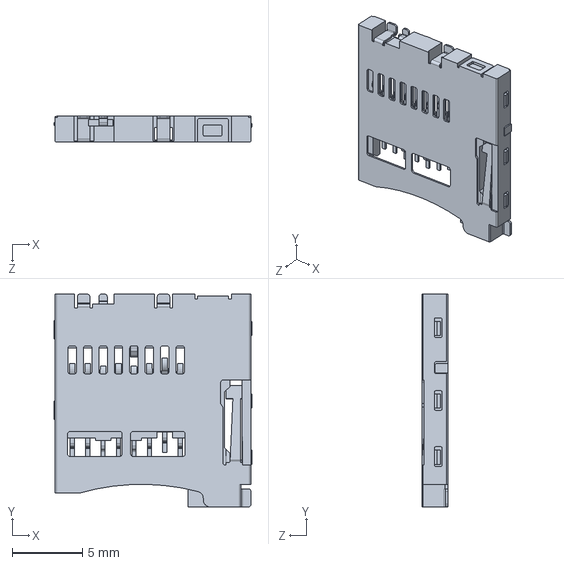
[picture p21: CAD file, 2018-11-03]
Board3 - Shorty/Documents/Avionics Chassis/microSD.SLDPRT
14.1 x 15.2 x 1.88 mm

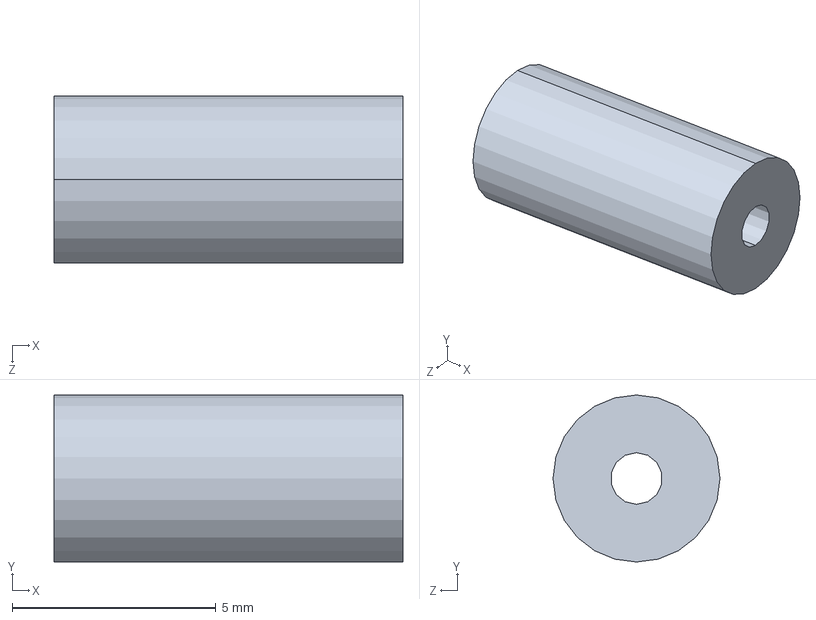
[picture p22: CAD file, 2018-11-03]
Board3 - Shorty/Documents/Avionics Chassis/132170/SMA7471B1-2T-50_1.sldprt
8.57 x 4.10 x 4.10 mm

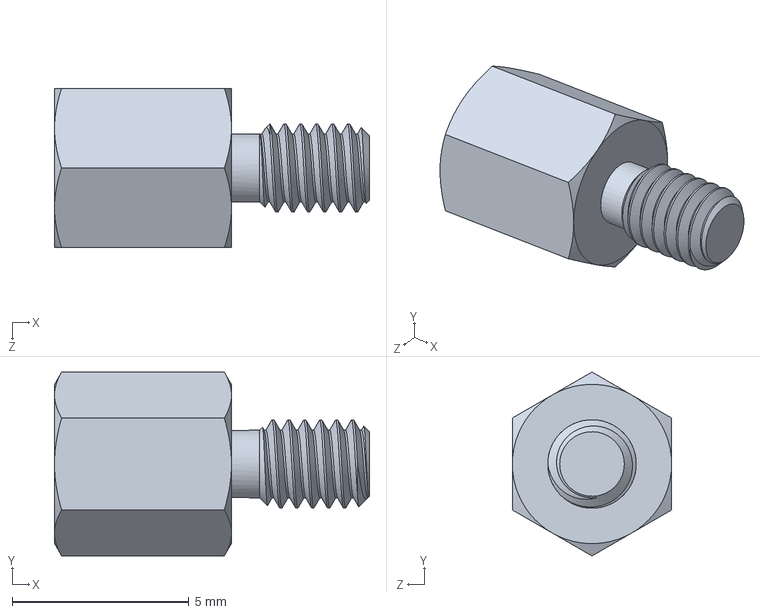
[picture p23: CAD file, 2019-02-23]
Test Rocket Avionics/Solidworks Models/5mm Standoff.SLDPRT
8.90 x 5.20 x 4.50 mm

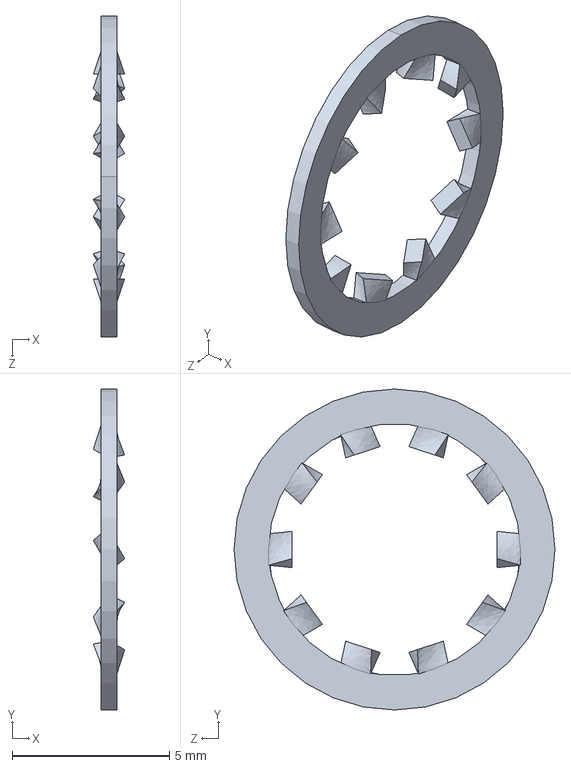
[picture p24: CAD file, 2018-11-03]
Board3 - Shorty/Documents/Avionics Chassis/132170/LW-102X65X05.sldprt
1.00 x 10.2 x 10.2 mm

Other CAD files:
Board3 - Shorty/Documents/avionicsboard.wrl_0.sldprt
Board5 - Circular Feather/Circular Avionics/circularm0 - avionicsprocessor.SLDPRT
Board3 - Shorty/Documents/avionicsboard.wrl.sldprt
Board3 - Shorty/Documents/bno055.wrl.sldprt
Board3 - Shorty/Documents/Avionics Board.stl
Board3 - Shorty/Documents/Avionics Chassis/132170/132170_3d_model_file.SLDASM
Board3 - Shorty/Documents/Avionics Chassis/132170/BD11ACS01A.sldprt
Board3 - Shorty/Documents/Avionics Chassis/132170/SMA termination - M.SLDPRT
Board3 - Shorty/Documents/Avionics Chassis/132170/SMA7471B1-2T-50.sldprt
Board3 - Shorty/Documents/Avionics Chassis/3318.SLDPRT
Board3 - Shorty/Documents/Avionics Chassis/3318.STEP
Board3 - Shorty/Documents/Avionics Chassis/3318.x_t
Board3 - Shorty/Documents/Avionics Chassis/473521001_microSD.stp
Board3 - Shorty/Documents/Avionics Chassis/AvionicBoard.SLDPRT
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

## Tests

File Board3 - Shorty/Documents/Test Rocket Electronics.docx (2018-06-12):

# Test Rocket Electronics

# Sensors

- ($10) Barometer (MPL3115A2) (https://www.adafruit.com/product/1893)
- ($35) IMU (BNO055) (https://www.adafruit.com/product/2472)
- ($0) Temperature (from the baro)
- ($16) GPS (https://www.amazon.com/MakerFocus-Microcontroller-Compatible-Navigation-Positioning/dp/B075DD5746)
- ($14) RTC (https://www.adafruit.com/product/3013)

# Radio

- 2x ($20) RFM95W LoRa Tranciever (https://www.adafruit.com/product/3072)icad

# Microcontroller

- ($20) Feather M0 (https://www.adafruit.com/product/2796)
- ($5) Mini USB Cable (https://www.amazon.com/AmazonBasics-USB-2-0-Cable-Male/dp/B00NH13S44)

# Power

- ($15) 7.2v 2S Battery (https://hobbyking.com/en_us/turnigy-nano-tech-2200mah-2s-35-70c-lipo-pack.html)
- ($12) Step Down (takes 7.v to 3.3v) (https://www.amazon.com/eBoot-LM2596-Converter-3-0-40V-1-5-35V/dp/B01GJ0SC2C)

# Misc

- ($10) Breadboard (https://www.amazon.com/Elegoo-EL-CP-003-Breadboard-Solderless-Distribution/dp/B01EV6LJ7G)
- ($15) Wires (https://www.amazon.com/CIRCUIT-TEST-Preformed-Breadboard-Jumper-Wire/dp/B008MOLG04?s=industrial)

# Airbrakes

- ($40) 120 Degree Servo (https://www.pololu.com/product/3429)

Total Cost: $223

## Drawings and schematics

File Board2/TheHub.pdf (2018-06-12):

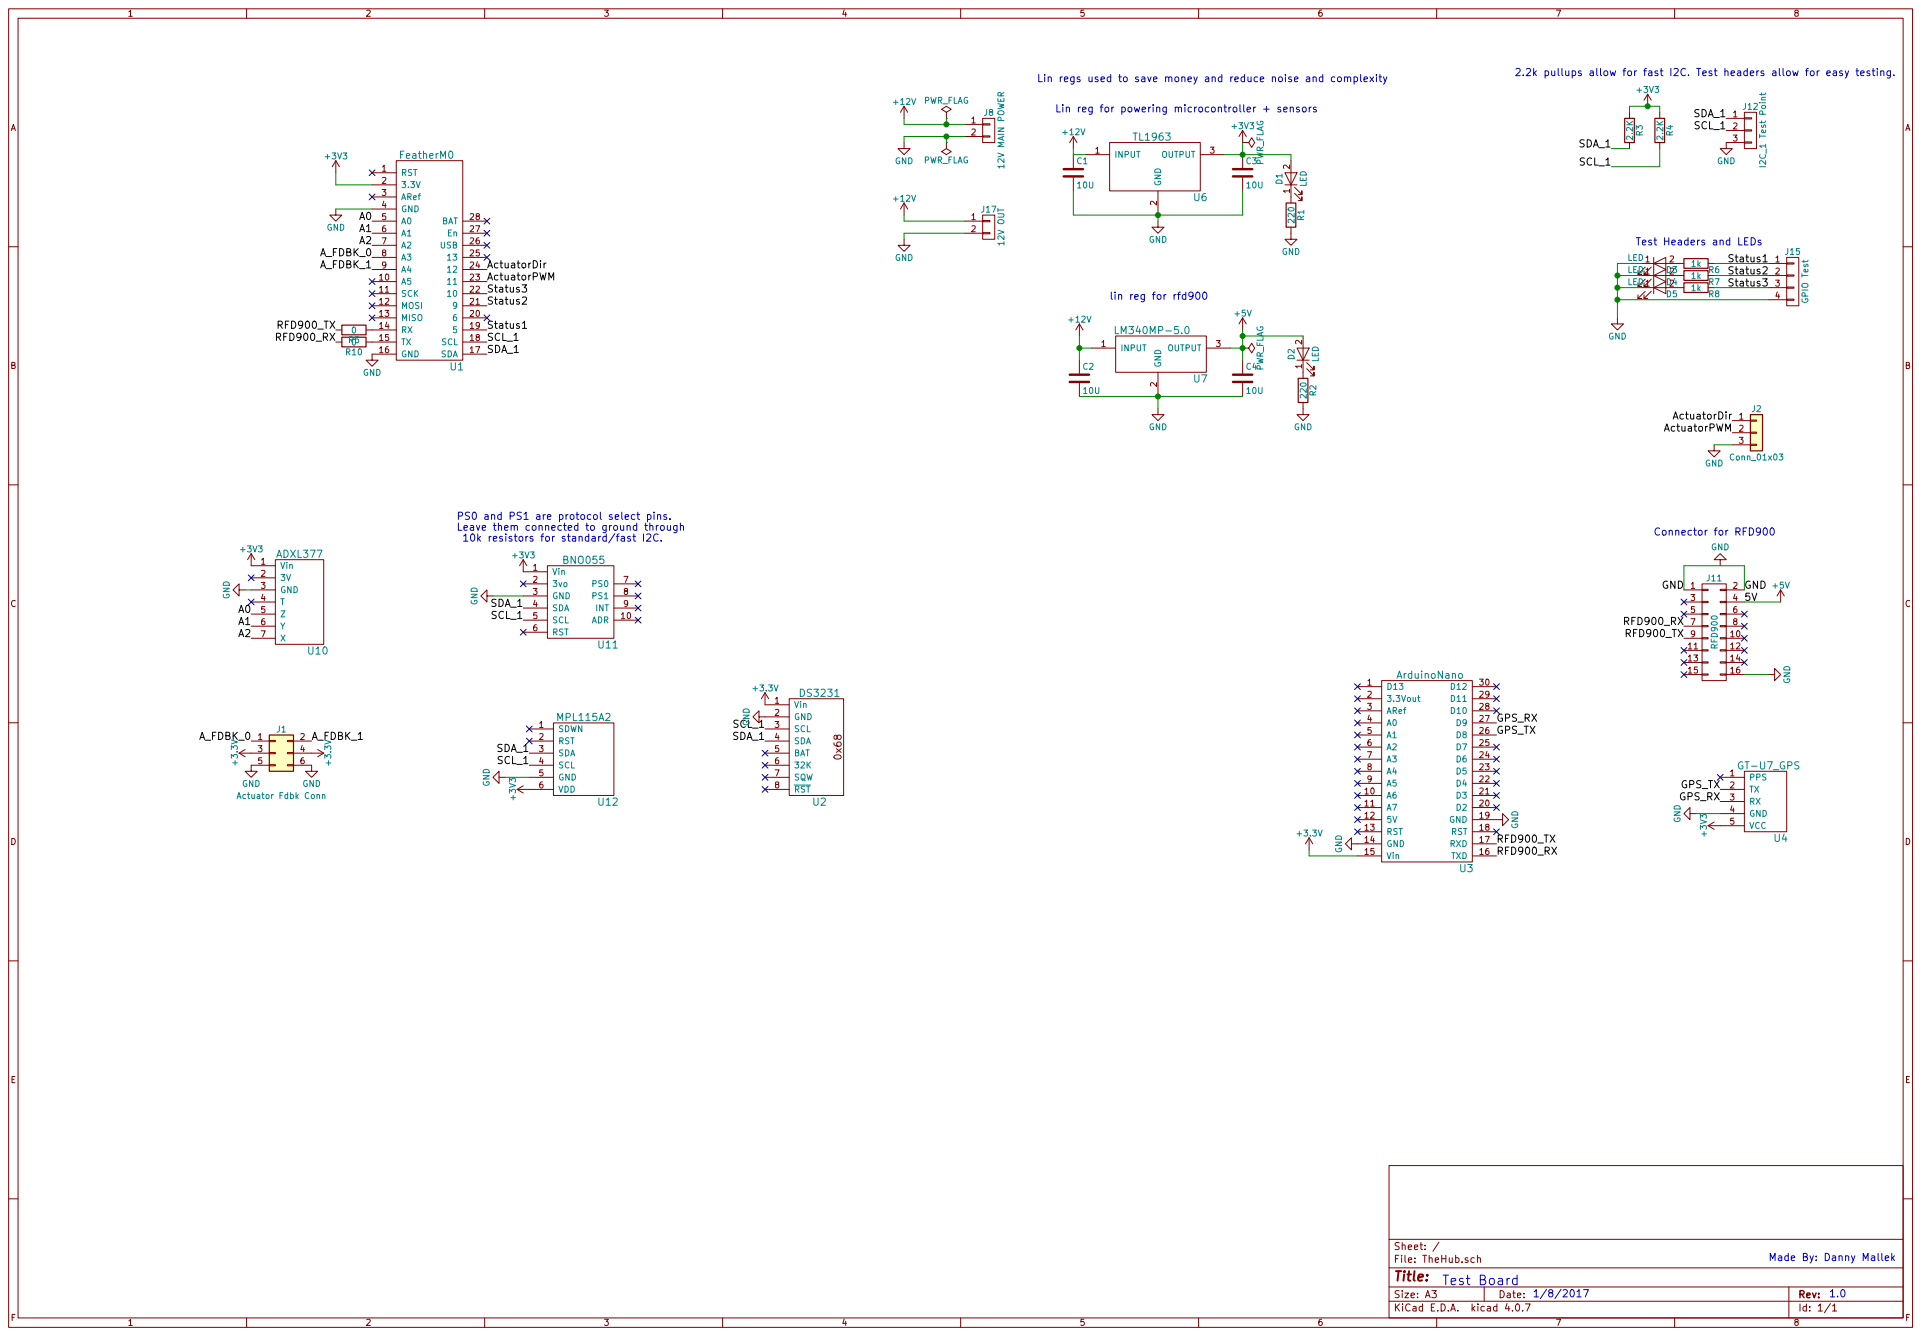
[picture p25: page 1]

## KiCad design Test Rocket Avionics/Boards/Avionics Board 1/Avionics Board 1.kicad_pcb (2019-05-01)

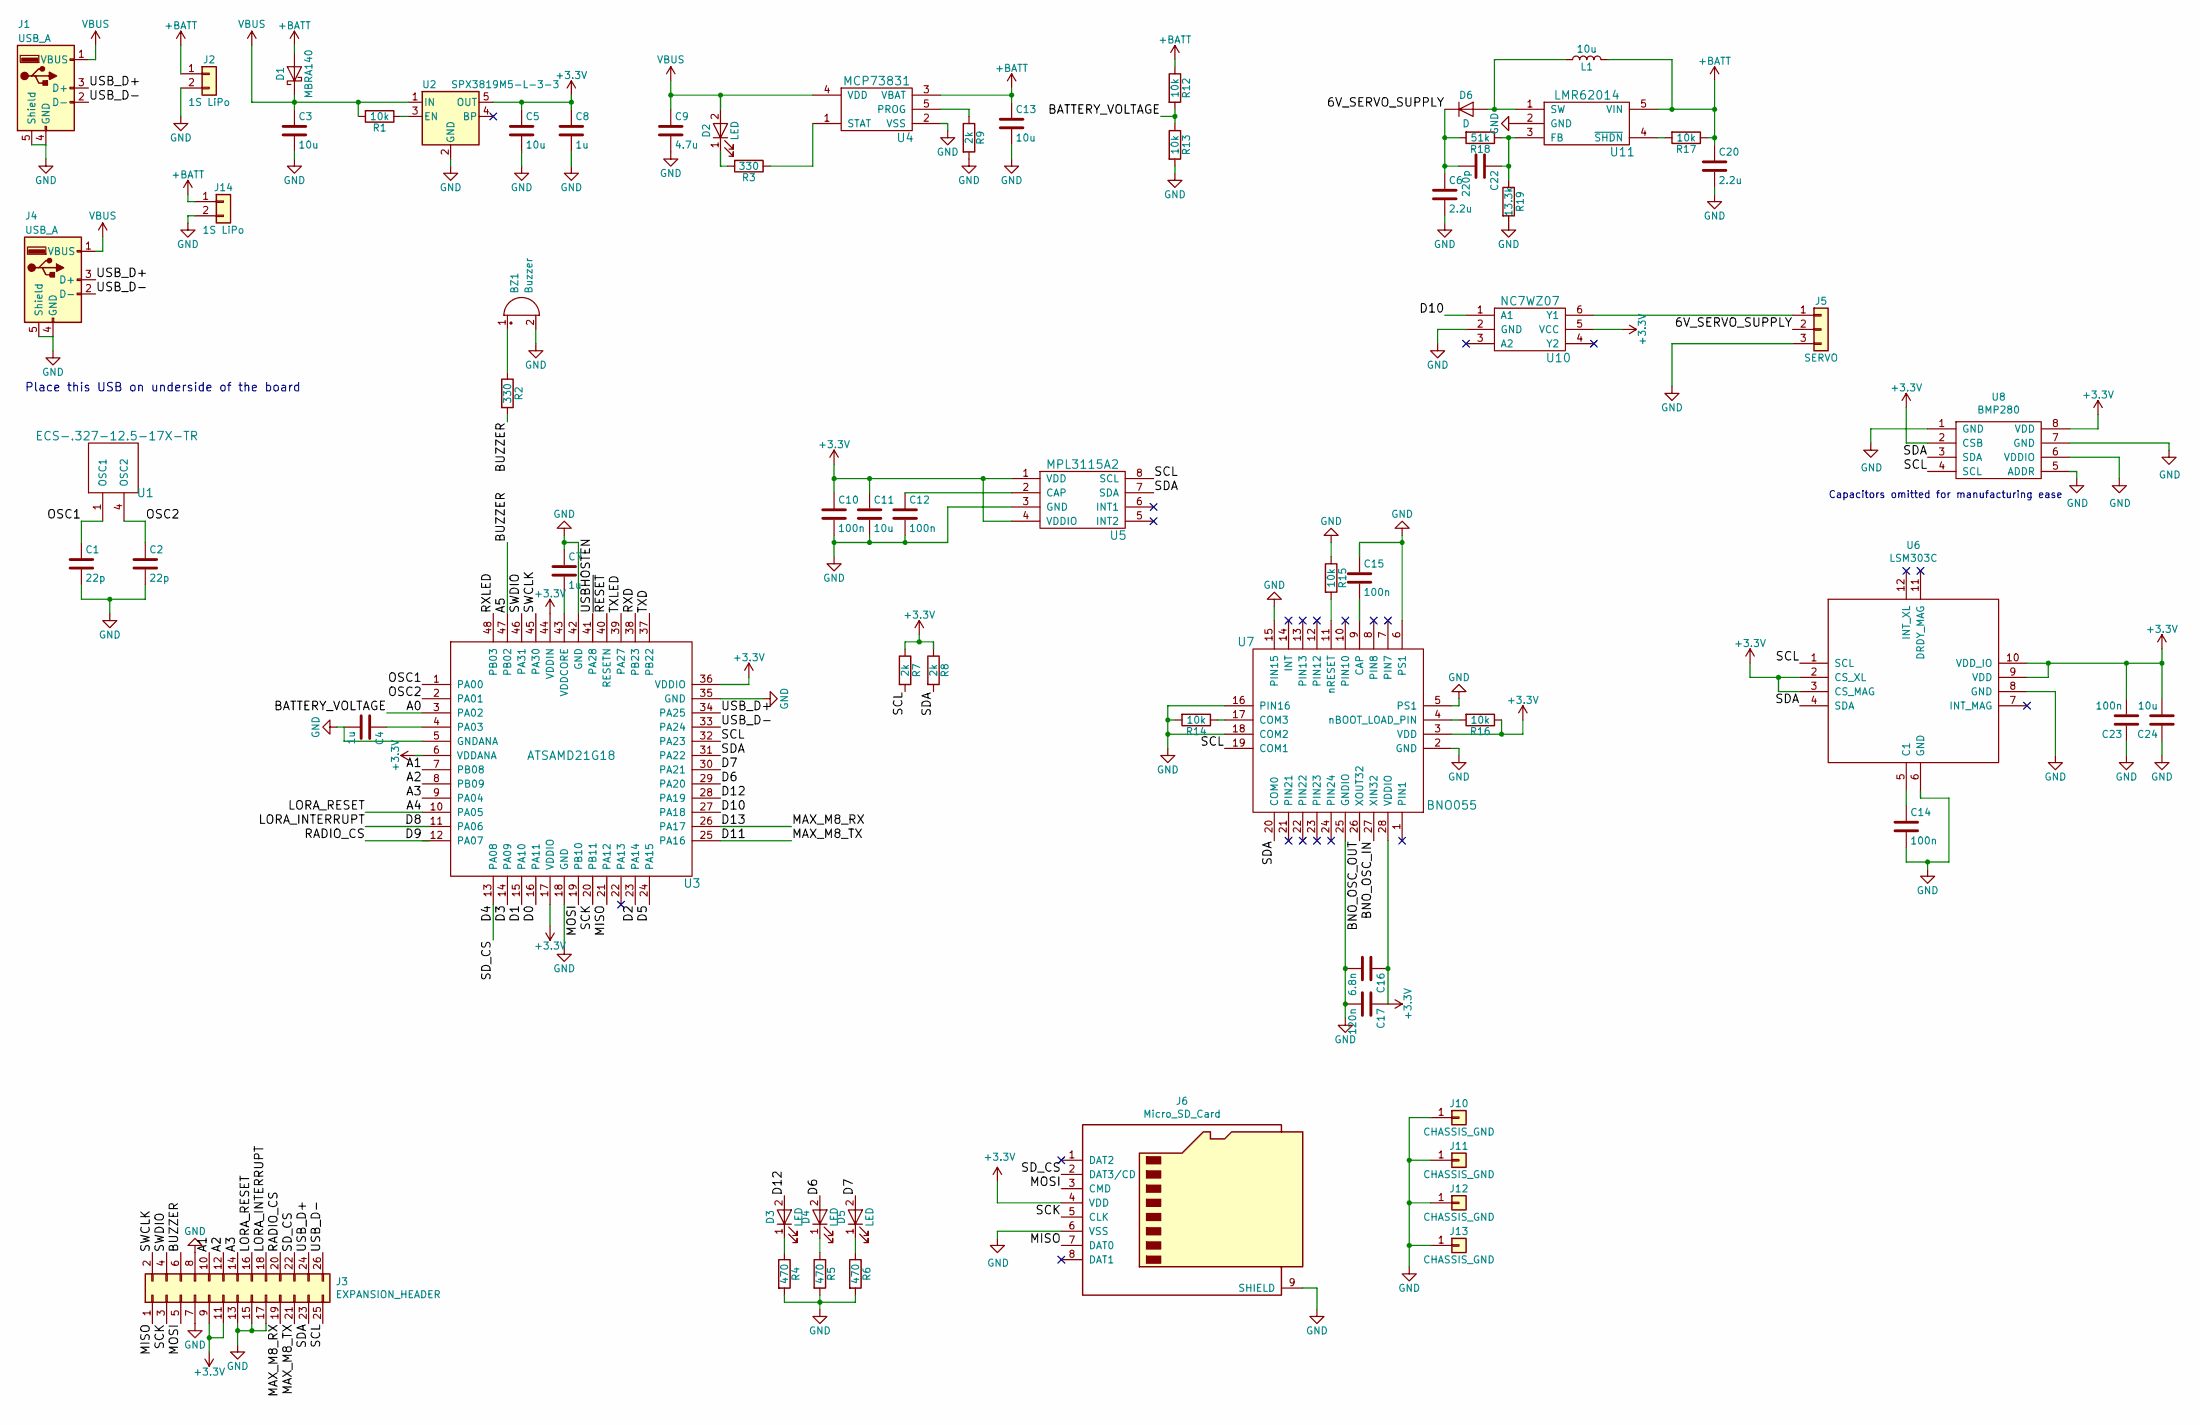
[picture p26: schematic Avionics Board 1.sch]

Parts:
BZ1: Buzzer; CUI_CMT-5023S-SMT
C1, C2: 22p; C_0805
C3, C5, C11, C13, C24: 10u; C_1206
C4, C7, C8: 1u; C_0805
C6, C20: 2.2u; C_1206
C9: 4.7u; C_1206
C10, C12, C14, C15, C23: 100n; C_0805
C16: 6.8n; C_0805
C17: 120n; C_0805
C22: 220p; C_0805
D1: MBRA140; DO-214AC
D2, D3, D4, D5: LED; D_0603
D6: D; D_SOD-123F
J1, J4: USB_A; USB_Mini-B
J2: 1S LiPo; JST-PH2
J3: EXPANSION_HEADER; Pin_Header_Straight_2x13_Pitch1.00mm
J5: SERVO; Pin_Header_Straight_1x03_Pitch2.54mm
J6: Micro_SD_Card; MicroSD_DM3D-SF
J10, J11, J12, J13: CHASSIS_GND; MountingHole_2.7mm_M2.5_Pad
J14: 1S LiPo; Pin_Header_Straight_1x02_Pitch2.54mm
L1: 10u; L_Wuerth_HCI-5040
R1, R12, R13, R14, R15, R16, R17: 10k; R_0805
R2, R3: 330; R_0805
R4, R5, R6: 470; R_0805
R7, R8, R9: 2k; R_0805
R18: 51k; R_0805
R19: 13.3k; R_0805
U1: ECS-.327-12.5-17X-TR; XC1195CT-ND
U2: SPX3819M5-L-3-3; SOT-23-5
U3: ATSAMD21G18; TQFP-48_7x7mm_Pitch0.5mm
U4: MCP73831; TSOT-23-5
U5: MPL3115A2
U6: LSM303C; LGA-12_2x2mm_Pitch0.5mm
U7: BNO055; BNO055-LGA
U8: BMP280
U10: NC7WZ07; SOT-363_SC-70-6
U11: LMR62014; SOT-23-5

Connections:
+3V3: C5.1, C8.1, C10.1, C11.1, C16.1, C17.1, C23.2, C24.2, J3.9, J3.11, J6.4 (VDD), R7.1, R8.1, R16.1, U2.5 (OUT), U3.6 (VDDANA), U3.17 (VDDIO), U3.36 (VDDIO), U3.44 (VDDIN), U5.1 (VDD), U5.4 (VDDIO), U6.2 (CS_XL), U6.3 (CS_MAG), U6.9 (VDD), U6.10 (VDD_IO), U7.3 (VDD), U7.28 (VDDIO), U8.2 (CSB), U8.8 (VDD), U10.5 (VCC)
+BATT: C13.1, C20.1, D1.2 (A), J2.1, J14.1, L1.2, R12.1, R17.1, U4.3 (VBAT), U11.5 (VIN)
/6V_SERVO_SUPPLY: C6.1, C22.2, D6.1 (K), J5.2, R18.2; also elsewhere on the board
/A0: R12.2, R13.1, U3.3 (PA02)
/A1: J3.10, U3.7 (PB08)
/A2: J3.12, U3.8 (PB09)
/A3: J3.14, U3.9 (PA04)
/A4: J3.16, U3.10 (PA05)
/A5: J3.6, R2.2, U3.47 (PB02)
/BNO_OSC_IN: U7.27 (XIN32)
/BNO_OSC_OUT: U7.26 (XOUT32)
/D0: U3.16 (PA11)
/D1: U3.15 (PA10)
/D2: U3.23 (PA14)
/D3: U3.14 (PA09)
/D4: J3.22, J6.2 (DAT3/CD), U3.13 (PA08)
/D5: U3.24 (PA15)
/D6: D4.2 (A), U3.29 (PA20)
/D7: D5.2 (A), U3.30 (PA21)
/D8: J3.18, U3.11 (PA06)
/D9: J3.20, U3.12 (PA07)
/D10: U3.27 (PA18), U10.1 (A1)
/D11: J3.21, U3.25 (PA16)
/D12: D3.2 (A), U3.28 (PA19)
/D13: J3.19, U3.26 (PA17)
/MISO: J3.1, J6.7 (DAT0), U3.21 (PA12)
/MOSI: J3.5, J6.3 (CMD), U3.19 (PB10)
/OSC1: C1.1, U1.1 (OSC1), U3.1 (PA00)
/OSC2: C2.1, U1.4 (OSC2), U3.2 (PA01)
/RXD: U3.38 (PB23)
/RXLED: U3.48 (PB03)
/SCK: J3.3, J6.5 (CLK), U3.20 (PB11)
/SCL: J3.25, R7.2, U3.32 (PA23), U5.8 (SCL), U6.1 (SCL), U7.19 (COM1), U8.4 (SCL)
/SDA: J3.23, R8.2, U3.31 (PA22), U5.7 (SDA), U6.4 (SDA), U7.20 (COM0), U8.3 (SDA)
/SWCLK: J3.2, U3.45 (PA30)
/SWDIO: J3.4, U3.46 (PA31)
/TXD: U3.37 (PB22)
/TXLED: U3.39 (PA27)
/USBHOSTEN: U3.41 (PA28)
/USB_D+: J1.3 (D+), J3.24, J4.3 (D+), U3.34 (PA25)
/USB_D-: J1.2 (D-), J3.26, J4.2 (D-), U3.33 (PA24)
/~RESET: U3.40 (RESETN)
GND: BZ1.2 (+), C1.2, C2.2, C3.2, C4.2, C5.2, C6.2, C7.1, C8.2, C9.2, C10.2, C11.2, C12.2, C13.2, C14.2, C15.1, C16.2, C17.2, C20.2, C23.1, C24.1, J1.4 (GND), J1.5 (Shield), J2.2, J3.7, J3.8, J3.13, J3.15, J3.17, J4.4 (GND), J4.5 (Shield), J5.3, J6.6 (VSS), J6.9 (SHIELD), J10.1, J11.1, J12.1, J13.1, J14.2, R4.2, R5.2, R6.2, R9.2, R13.2, R14.2, R15.1, R19.2, U2.2 (GND), U3.5 (GNDANA), U3.18 (GND), U3.35 (GND), U3.42 (GND), U4.2 (VSS), U5.3 (GND), U6.6 (GND), U6.8 (GND), U7.2 (GND), U7.5 (PS1), U7.6 (PS1), U7.15 (PIN15), U7.16 (PIN16), U7.18 (COM2), U7.25 (GNDIO), U8.1 (GND), U8.5 (ADDR), U8.6 (VDDIO), U8.7 (GND), U10.2 (GND), U11.2 (GND)
unnamed: BZ1.1 (-), R2.1
unnamed: C4.1, U3.4 (PA03)
unnamed: C7.2, U3.43 (VDDCORE)
unnamed: C12.1, U5.2 (CAP)
unnamed: C14.1, U6.5 (C1)
unnamed: C15.2, U7.9 (CAP)
unnamed 49: C22.1, R18.1, R19.1, U11.3 (FB); also elsewhere on the board
unnamed: D2.1 (K), R3.2
unnamed: D3.1 (K), R4.1
unnamed: D4.1 (K), R5.1
unnamed: D5.1 (K), R6.1
unnamed: D6.2 (A), L1.1, U11.1 (SW)
unnamed: J5.1, U10.6 (Y1)
unnamed: R1.1, U2.3 (EN)
unnamed: R3.1, U4.1 (STAT)
unnamed: R9.1, U4.5 (PROG)
unnamed: R14.1, U7.17 (COM3)
unnamed: R15.2, U7.11 (nRESET)
unnamed: R16.2, U7.4 (nBOOT_LOAD_PIN)
unnamed: R17.2, U11.4 (~SHDN)
VBUS: C3.1, C9.1, D1.1 (K), D2.2 (A), J1.1 (VBUS), J4.1 (VBUS), R1.2, U2.1 (IN), U4.4 (VDD)

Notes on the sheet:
Place this USB on underside of the board
Capacitors omitted for manufacturing ease

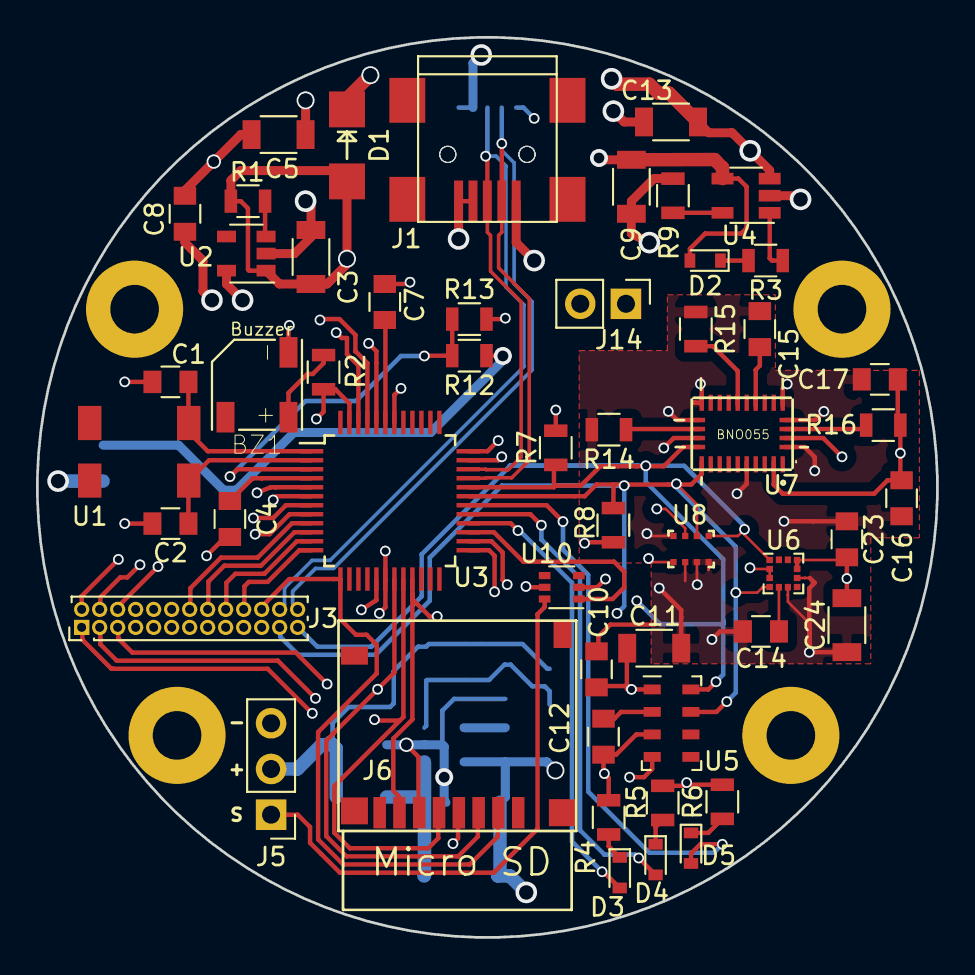
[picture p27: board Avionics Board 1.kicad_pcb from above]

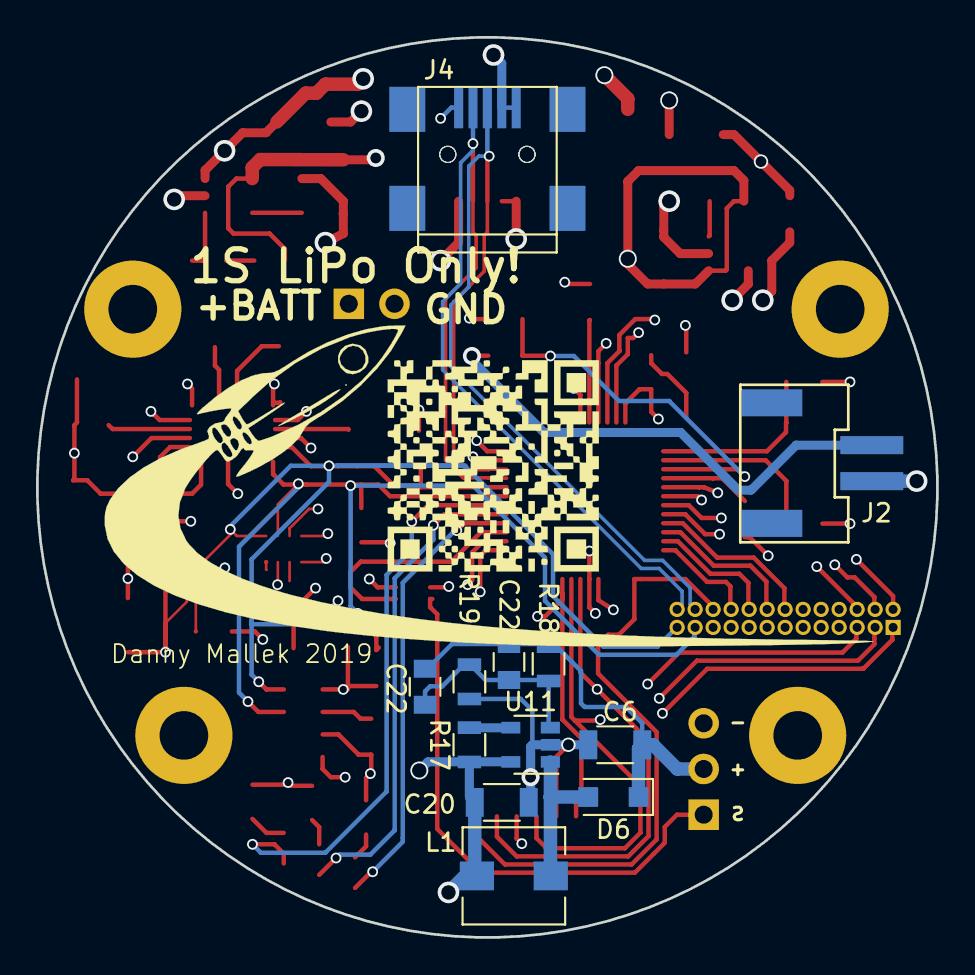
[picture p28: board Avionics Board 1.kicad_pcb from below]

Board: 4 copper layers, 50.0 x 50.0 mm, 68 parts (12 on the bottom side), 51 nets.

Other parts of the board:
C22#2: 220p; C_0805

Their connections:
/6V_SERVO_SUPPLY: C22#2.2; also elsewhere on the board
unnamed 49: C22#2.1; also elsewhere on the board

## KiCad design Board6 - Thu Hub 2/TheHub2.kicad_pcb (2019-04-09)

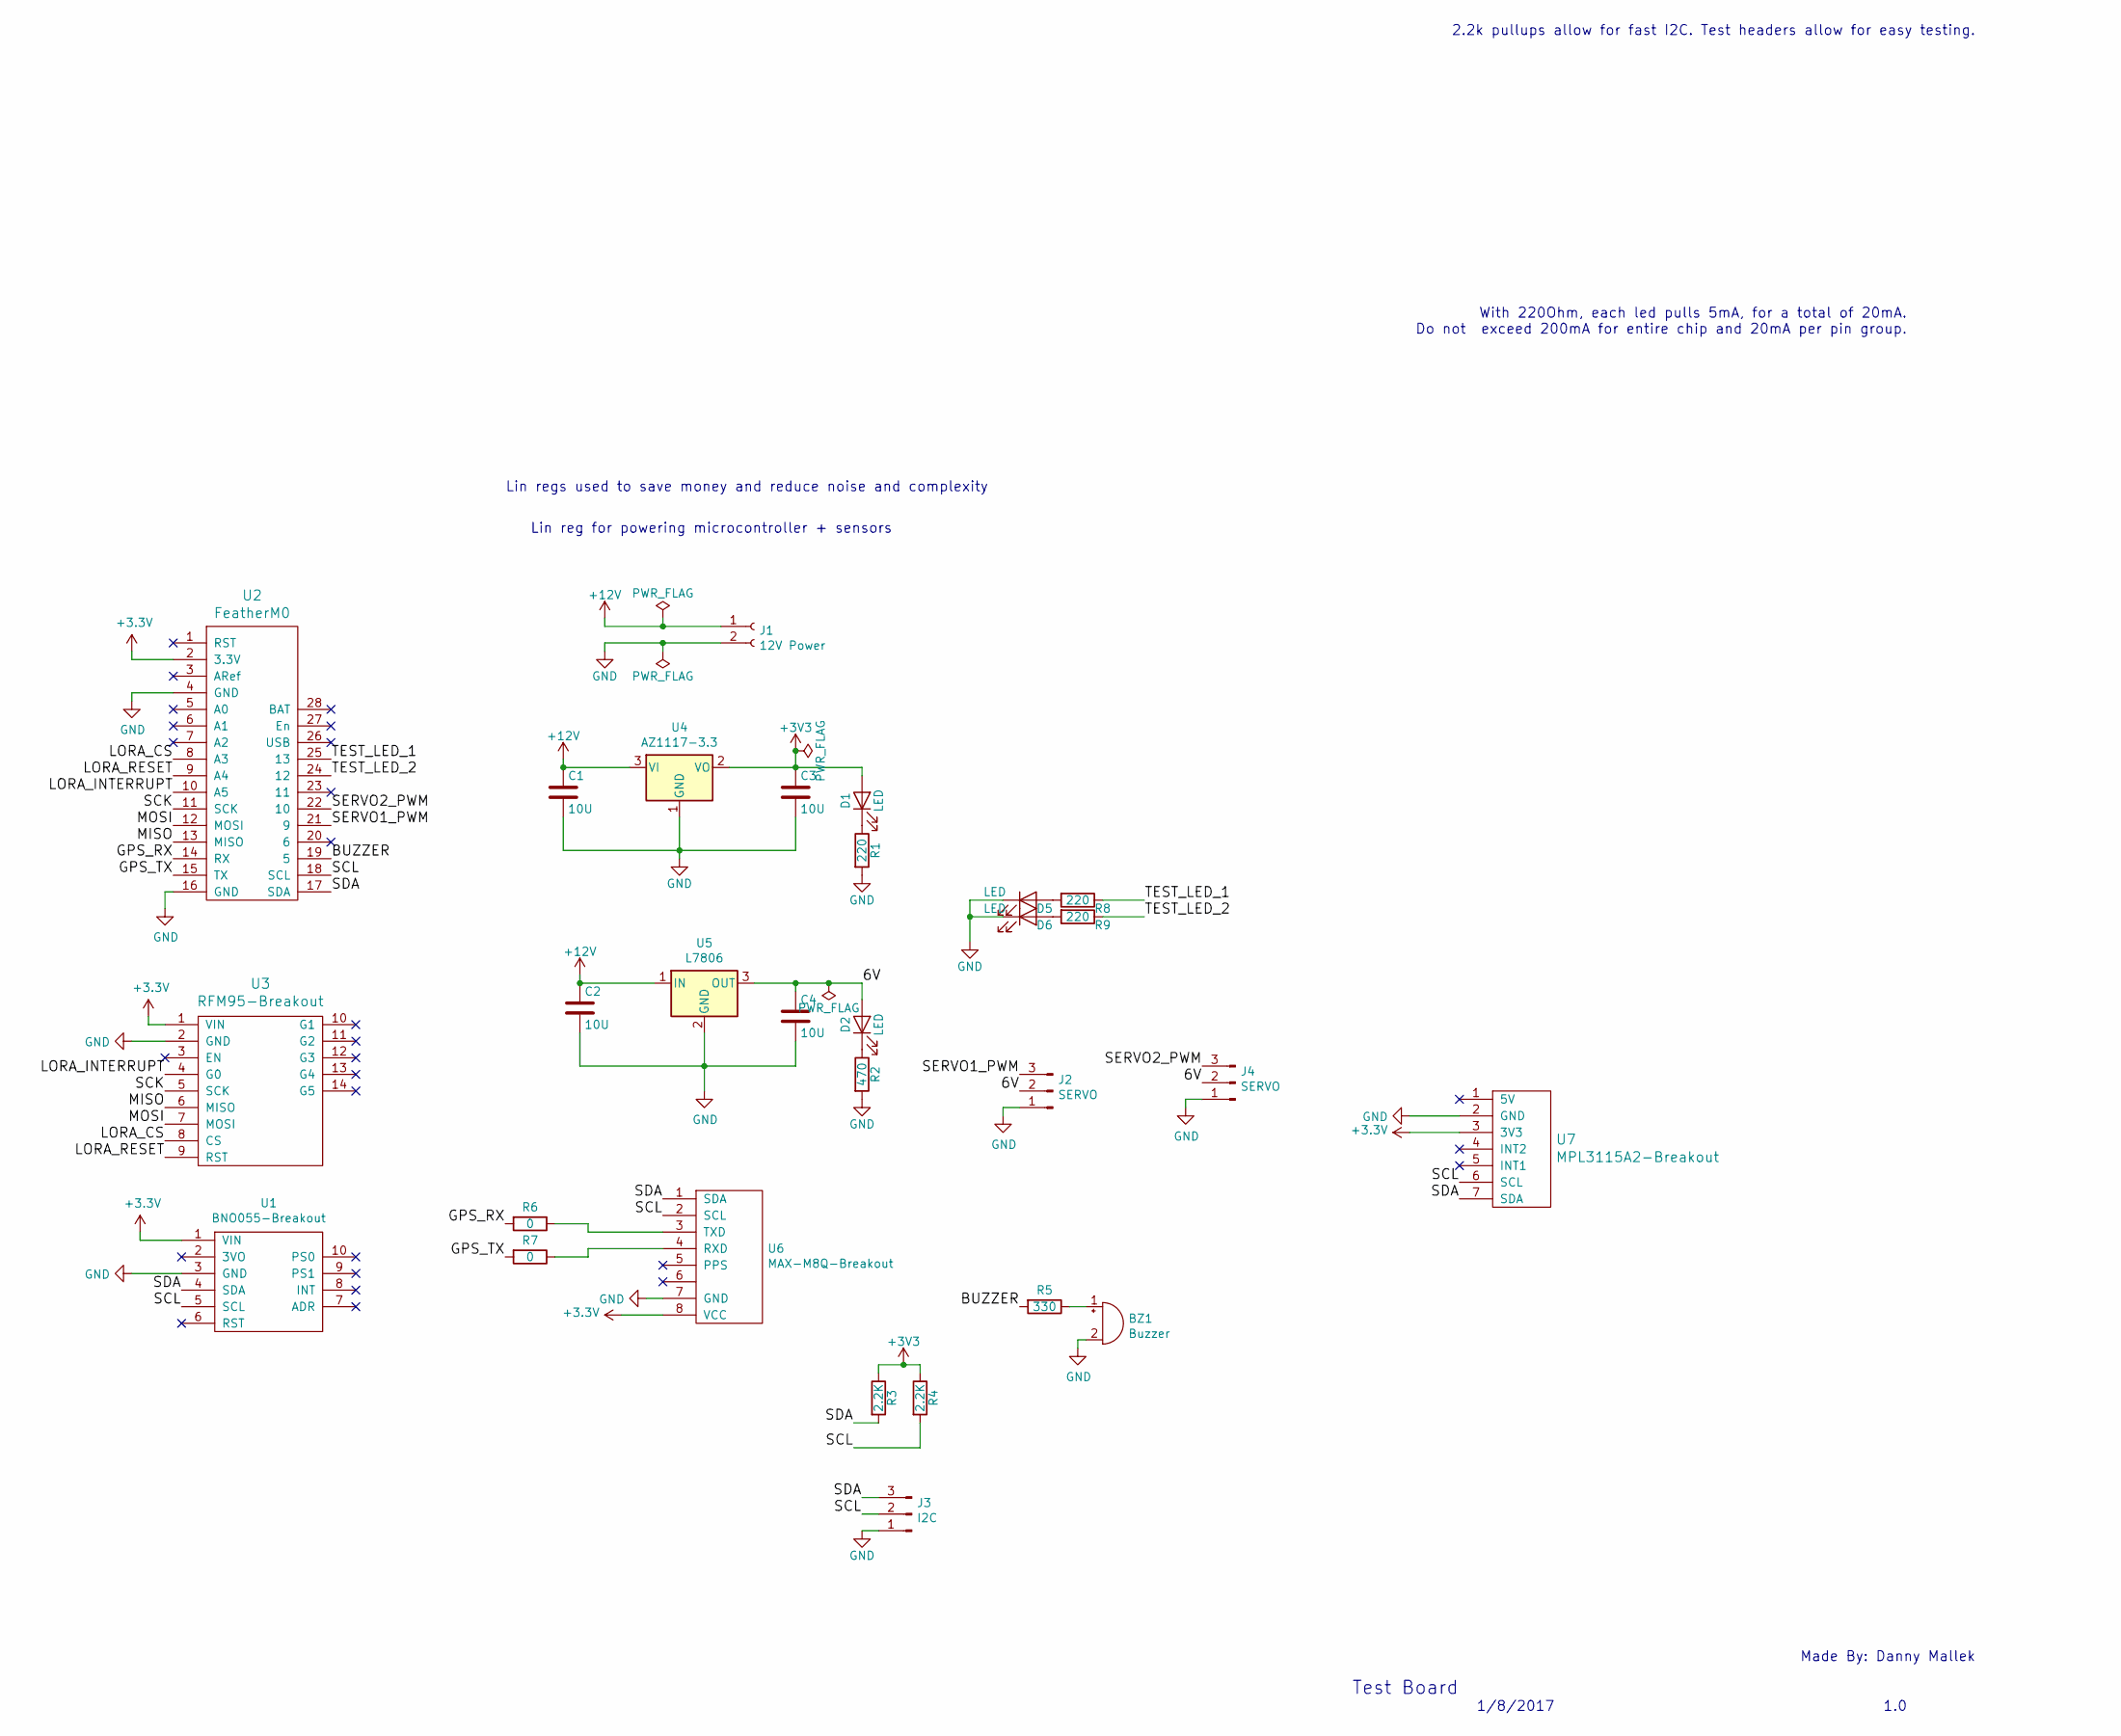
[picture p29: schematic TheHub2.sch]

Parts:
BZ1: Buzzer; CUI_CMT-5023S-SMT
C1, C2, C3, C4: 10U; C_0805
D1, D2, D5, D6: LED; LED_0805
J1: 12V Power; XT60
J2, J4: SERVO; Pin_Header_Straight_1x03_Pitch2.54mm
J3: I2C; Pin_Header_Straight_1x03_Pitch2.54mm
R1, R8, R9: 220; R_0805
R2: 470; R_0805
R3, R4: 2.2K; R_0805
R5: 330; R_0805
R6, R7: 0; R_0805
U1: BNO055-Breakout; BNO055
U2: FeatherM0; FEATHER-M0-DATALOGGER
U3: RFM95-Breakout
U4: AZ1117-3.3; SOT-223-3_TabPin2
U5: L7806; TO-263-2
U6: MAX-M8Q-Breakout
U7: MPL3115A2-Breakout

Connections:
+12V: C1.1, C2.1, J1.1, U4.3 (VI), U5.1 (IN)
/6V: C4.1, D2.2 (A), J2.2, J4.2, U5.3 (OUT)
/BUZZER: R5.2, U2.19 (5)
/GPS_RX: R6.2, U2.14 (RX)
/GPS_TX: R7.2, U2.15 (TX)
/LORA_CS: U2.8 (A3), U3.8 (CS)
/LORA_INTERRUPT: U2.10 (A5), U3.4 (G0)
/LORA_RESET: U2.9 (A4), U3.9 (RST)
/MISO: U2.13 (MISO), U3.6 (MISO)
/MOSI: U2.12 (MOSI), U3.7 (MOSI)
/SCK: U2.11 (SCK), U3.5 (SCK)
/SCL: J3.2, R4.2, U1.5 (SCL), U2.18 (SCL), U6.2 (SCL), U7.6 (SCL)
/SDA: J3.3, R3.2, U1.4 (SDA), U2.17 (SDA), U6.1 (SDA), U7.7 (SDA)
/SERVO1_PWM: J2.3, U2.21 (9)
/SERVO2_PWM: J4.3, U2.22 (10)
/TEST_LED_1: R8.1, U2.25 (13)
/TEST_LED_2: R9.1, U2.24 (12)
GND: BZ1.2 (+), C1.2, C2.2, C3.2, C4.2, D5.1 (K), D6.1 (K), J1.2, J2.1, J3.1, J4.1, R1.2, R2.2, U1.3 (GND), U2.4 (GND), U2.16 (GND), U3.2 (GND), U4.1 (GND), U5.2 (GND), U6.7 (GND), U7.2 (GND)
unnamed: BZ1.1 (-), R5.1
unnamed: D1.1 (K), R1.1
unnamed: D2.1 (K), R2.1
unnamed: D5.2 (A), R8.2
unnamed: D6.2 (A), R9.2
unnamed: R6.1, U6.3 (TXD)
unnamed: R7.1, U6.4 (RXD)

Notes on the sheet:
With 220Ohm, each led pulls 5mA, for a total of 20mA. Do not exceed 200mA for entire chip and 20mA per pin group.
Test Board
1.0
1/8/2017
Made By: Danny Mallek
2.2k pullups allow for fast I2C. Test headers allow for easy testing.
Lin reg for powering microcontroller + sensors
Lin regs used to save money and reduce noise and complexity

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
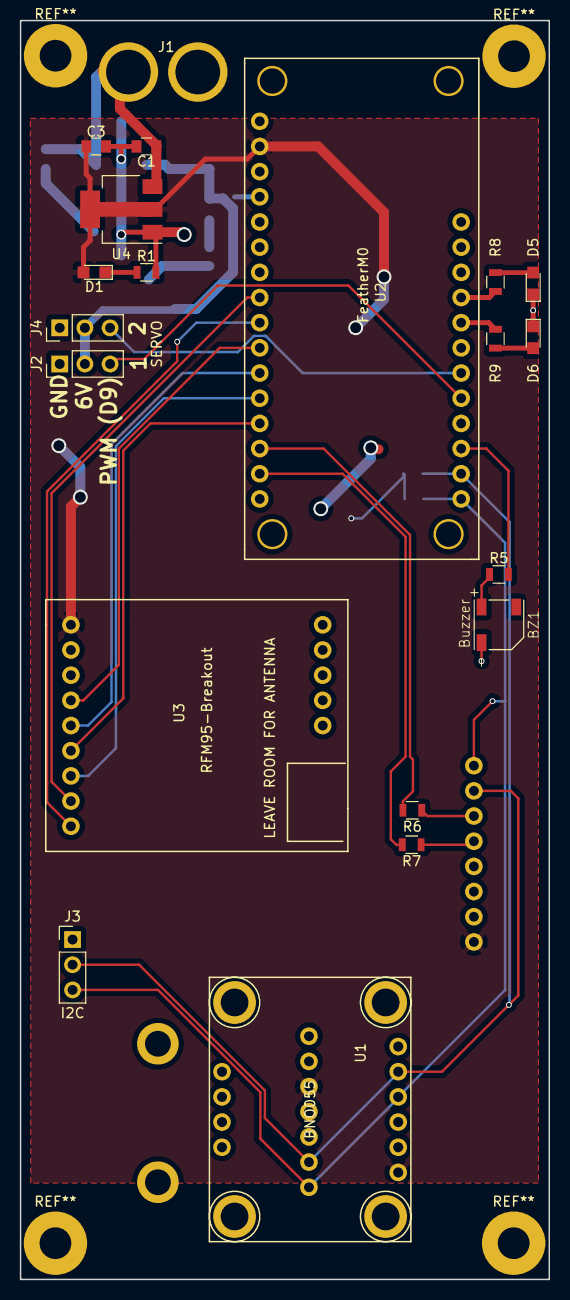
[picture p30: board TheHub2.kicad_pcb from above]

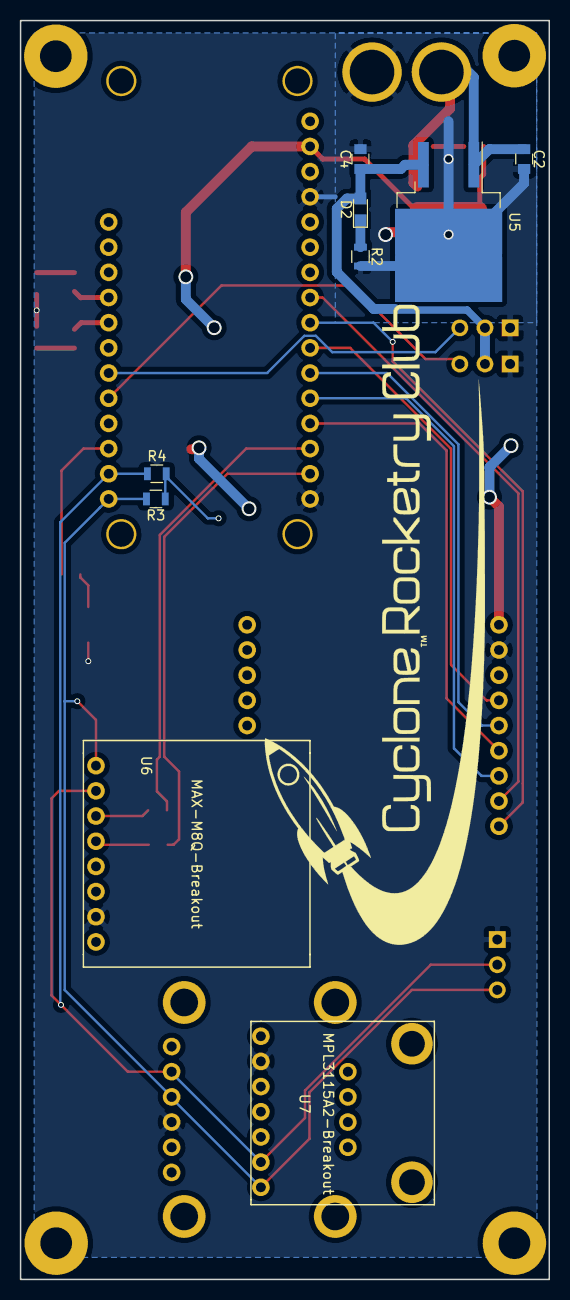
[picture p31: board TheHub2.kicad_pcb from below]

Board: 2 copper layers, 53.3 x 127.0 mm, 29 parts (9 on the bottom side), 26 nets.

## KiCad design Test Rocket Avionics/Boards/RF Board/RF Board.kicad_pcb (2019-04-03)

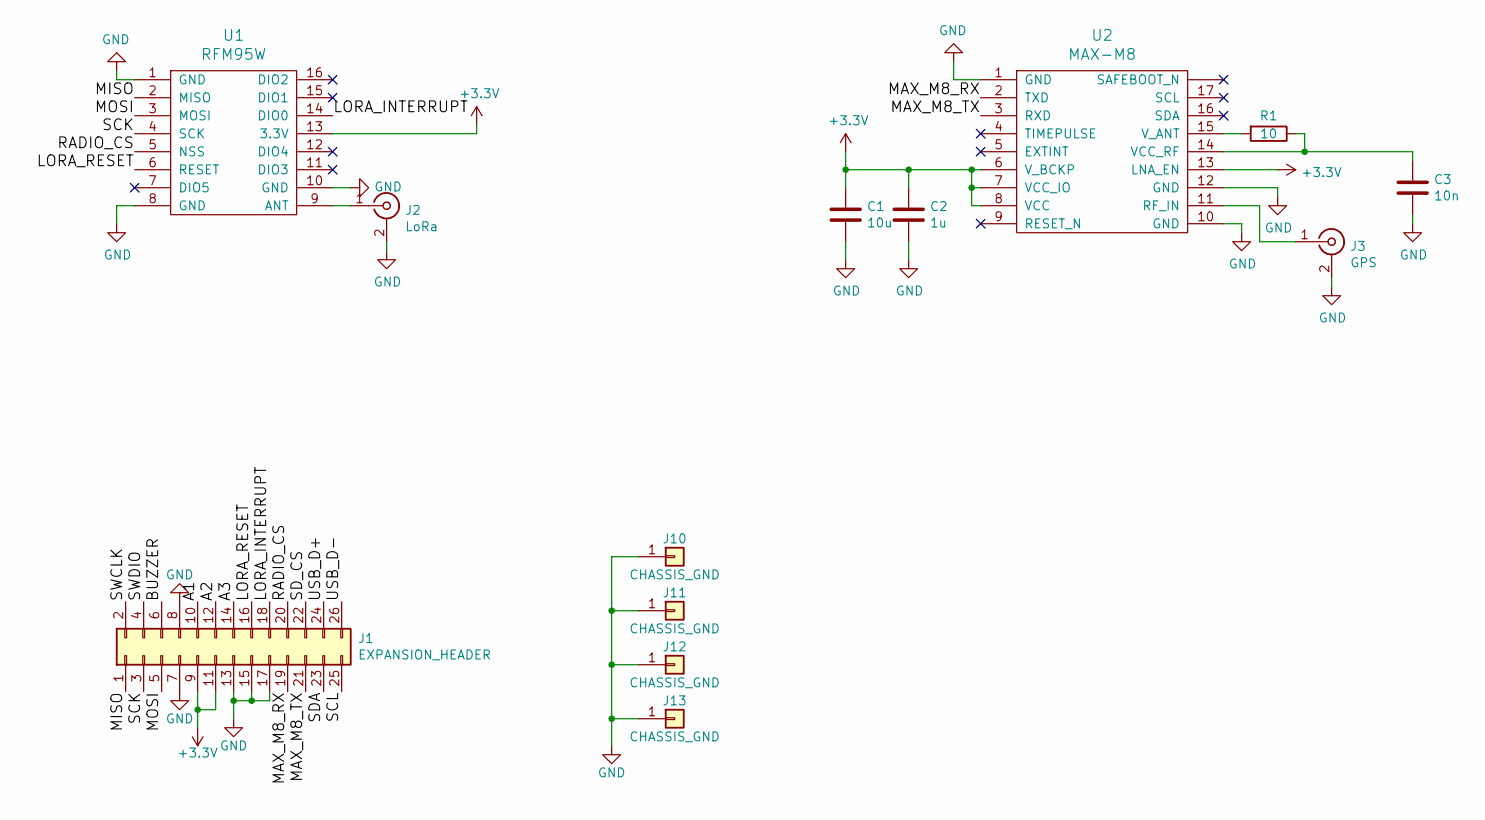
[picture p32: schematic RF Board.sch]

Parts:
C1: 10u; C_0805
C2: 1u; C_0805
C3: 10n; C_0805
J1: EXPANSION_HEADER; Pin_Header_Straight_2x13_Pitch1.00mm
J2: LoRa; SMA_TH
J3: GPS; SMA_TH
J10, J11, J12, J13: CHASSIS_GND; MountingHole_2.7mm_M2.5_Pad
R1: 10; R_0805
U1: RFM95W
U2: MAX-M8; MAX_M82

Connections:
+3V3: C1.1, C2.1, J1.9, J1.11, U1.13 (3.3V), U2.6 (V_BCKP), U2.7 (VCC_IO), U2.8 (VCC), U2.13 (LNA_EN)
/A1: J1.10
/A2: J1.12
/A3: J1.14
/BUZZER: J1.6
/LORA_INTERRUPT: J1.18, U1.14 (DIO0)
/LORA_RESET: J1.16, U1.6 (RESET)
/MAX_M8_RX: J1.19, U2.2 (TXD)
/MAX_M8_TX: J1.21, U2.3 (RXD)
/MISO: J1.1, U1.2 (MISO)
/MOSI: J1.5, U1.3 (MOSI)
/RADIO_CS: J1.20, U1.5 (NSS)
/SCK: J1.3, U1.4 (SCK)
/SCL: J1.25
/SDA: J1.23
/SD_CS: J1.22
/SWCLK: J1.2
/SWDIO: J1.4
/USB_D+: J1.24
/USB_D-: J1.26
GND: C1.2, C2.2, C3.2, J1.7, J1.8, J1.13, J1.15, J1.17, J2.2 (Ext), J3.2 (Ext), J10.1, J11.1, J12.1, J13.1, U1.1 (GND), U1.8 (GND), U1.10 (GND), U2.1 (GND), U2.10 (GND), U2.12 (GND)
unnamed: C3.1, R1.1, U2.14 (VCC_RF)
unnamed: J2.1 (In), U1.9 (ANT)
unnamed: J3.1 (In), U2.11 (RF_IN)
unnamed: R1.2, U2.15 (V_ANT)

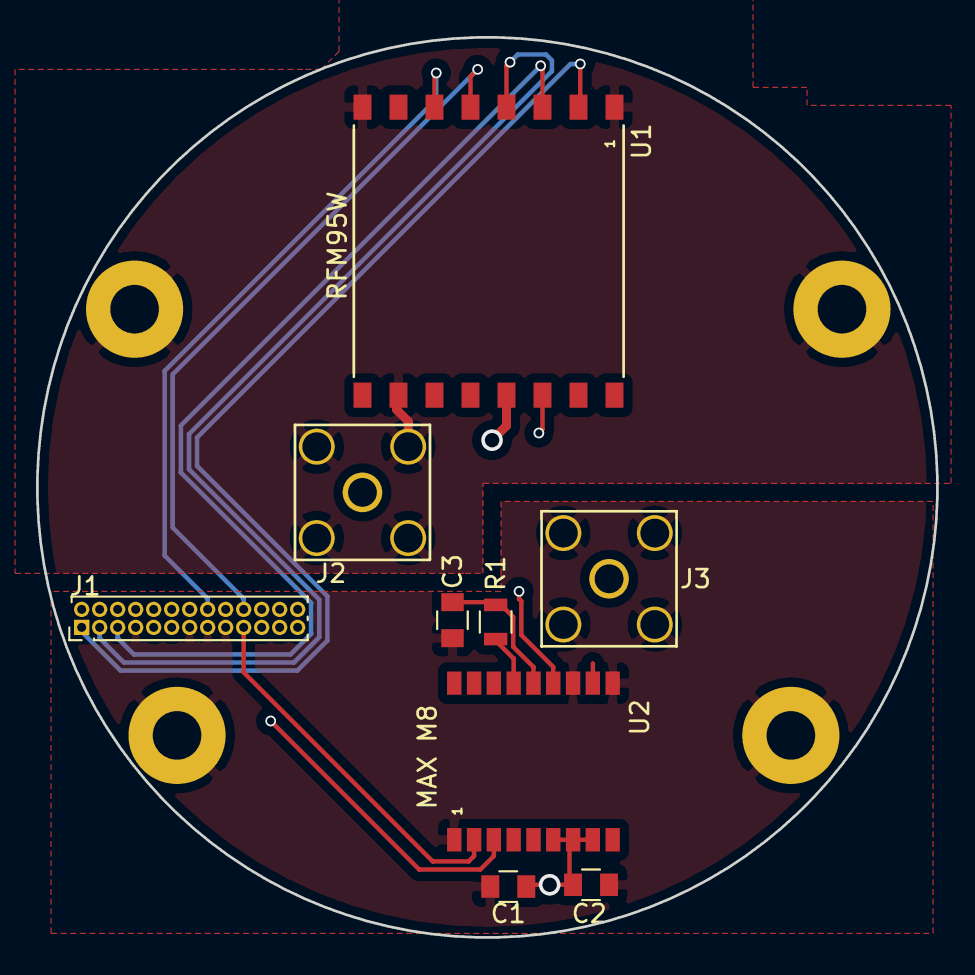
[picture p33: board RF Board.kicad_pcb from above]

Board: 4 copper layers, 50.0 x 50.0 mm, 13 parts (0 on the bottom side), 14 nets.

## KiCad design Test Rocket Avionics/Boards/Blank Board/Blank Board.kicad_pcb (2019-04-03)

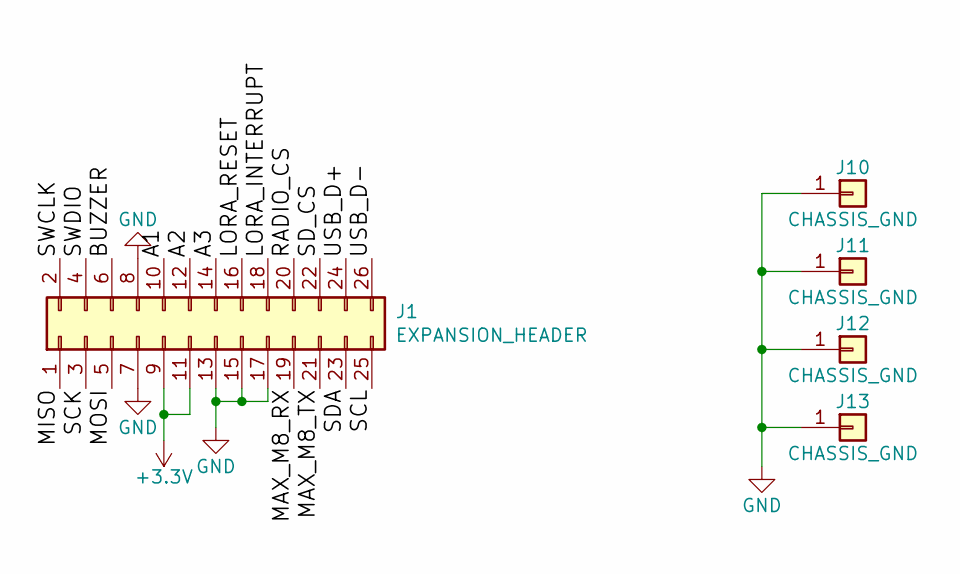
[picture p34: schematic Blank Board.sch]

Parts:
J1: EXPANSION_HEADER; Pin_Header_Straight_2x13_Pitch1.00mm
J10, J11, J12, J13: CHASSIS_GND; MountingHole_2.7mm_M2.5_Pad

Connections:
+3V3: J1.9, J1.11
/A1: J1.10
/A2: J1.12
/A3: J1.14
/BUZZER: J1.6
/LORA_INTERRUPT: J1.18
/LORA_RESET: J1.16
/MAX_M8_RX: J1.19
/MAX_M8_TX: J1.21
/MISO: J1.1
/MOSI: J1.5
/RADIO_CS: J1.20
/SCK: J1.3
/SCL: J1.25
/SDA: J1.23
/SD_CS: J1.22
/SWCLK: J1.2
/SWDIO: J1.4
/USB_D+: J1.24
/USB_D-: J1.26
GND: J1.7, J1.8, J1.13, J1.15, J1.17, J10.1, J11.1, J12.1, J13.1

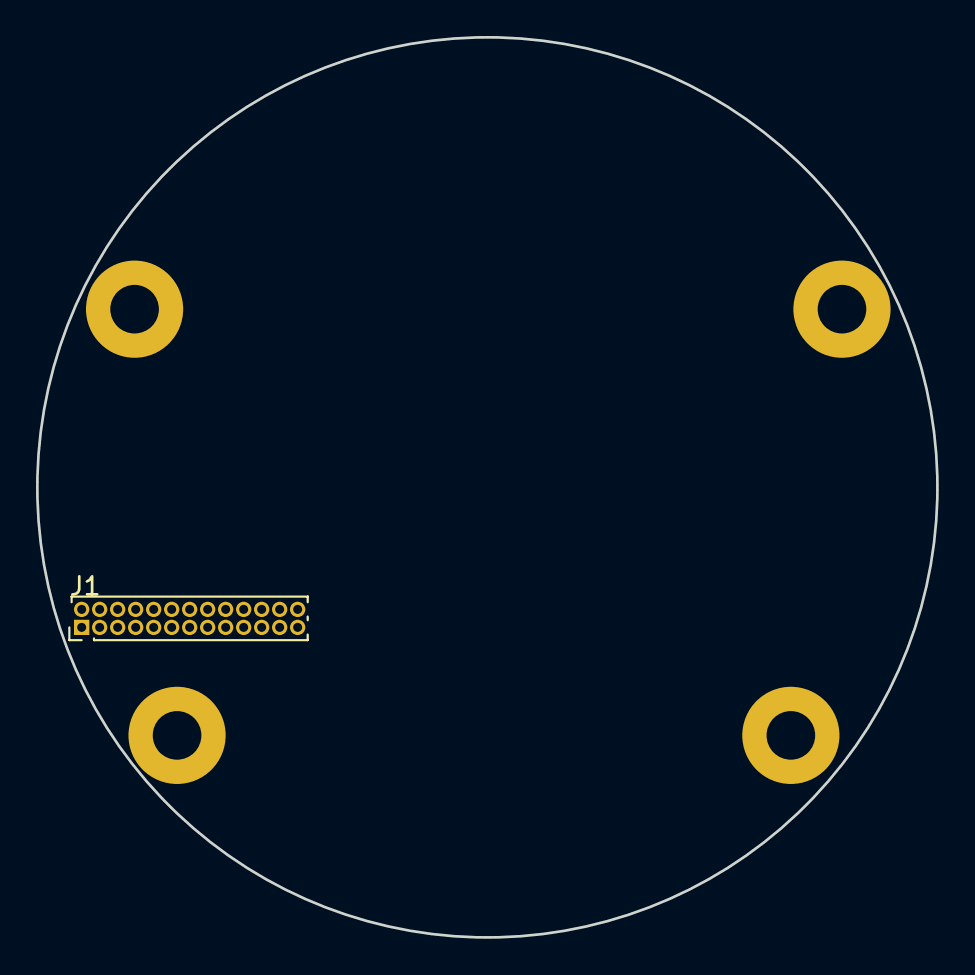
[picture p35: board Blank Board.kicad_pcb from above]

Board: 4 copper layers, 50.0 x 50.0 mm, 5 parts (0 on the bottom side), 2 nets.

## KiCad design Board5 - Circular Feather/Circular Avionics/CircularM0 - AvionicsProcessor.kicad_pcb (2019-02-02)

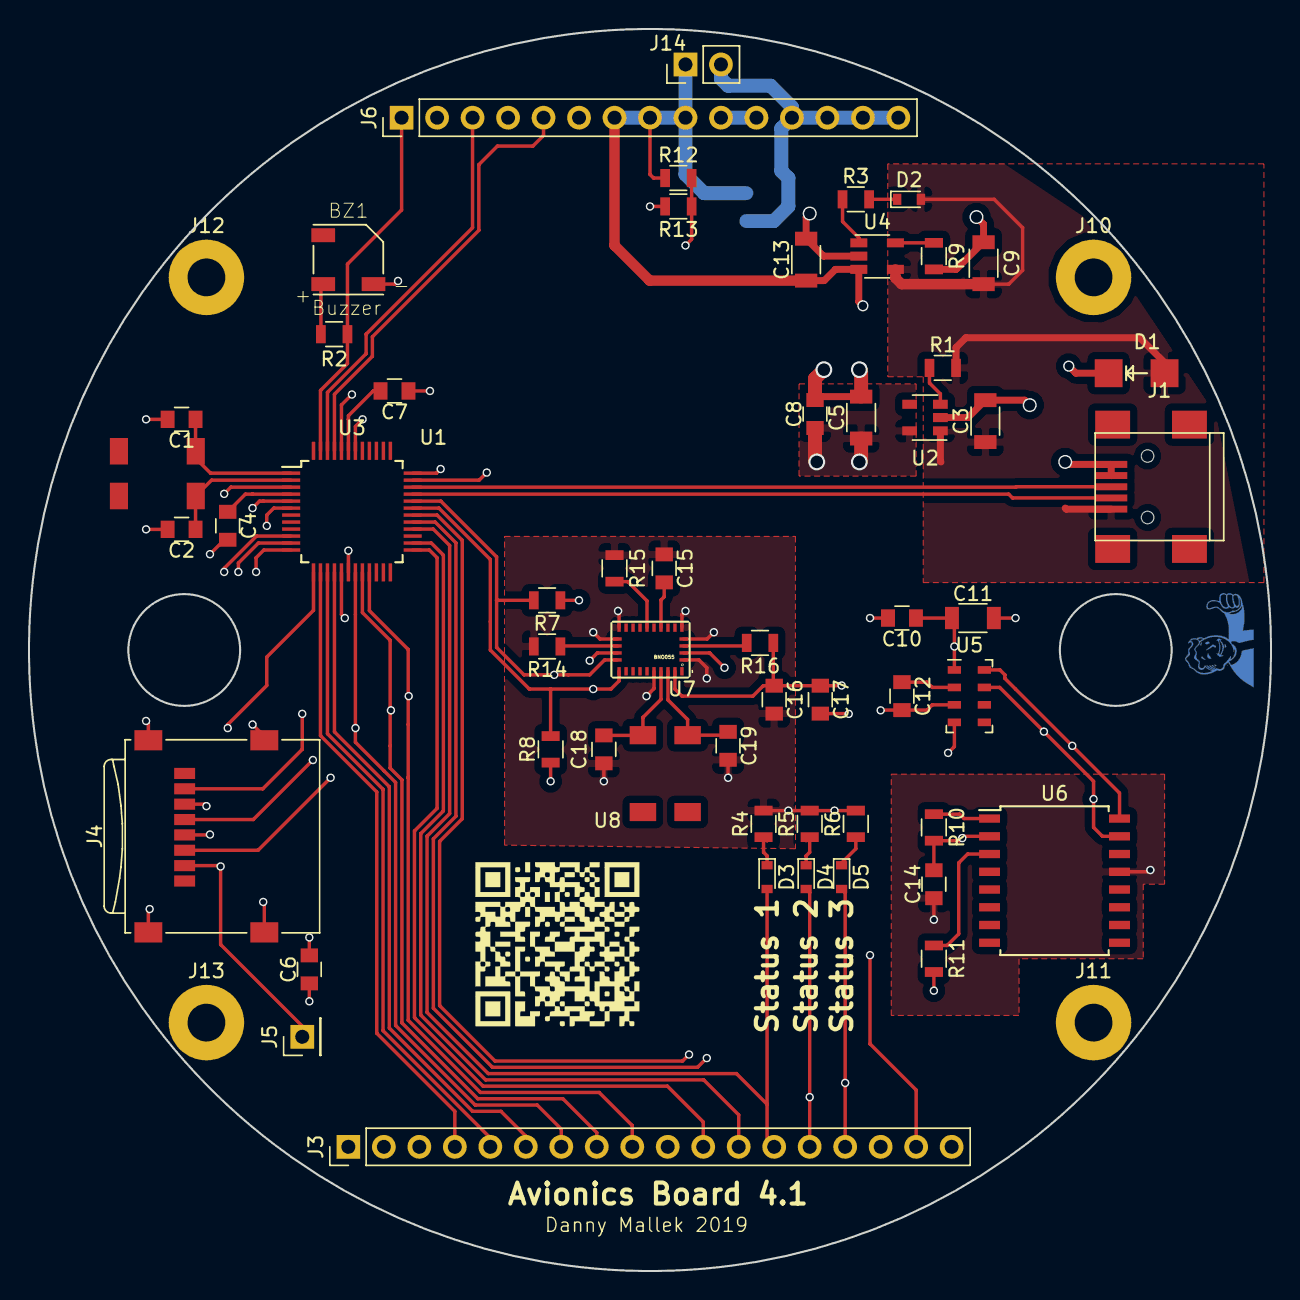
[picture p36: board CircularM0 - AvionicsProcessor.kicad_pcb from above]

Board: 4 copper layers, 88.9 x 88.9 mm, 60 parts (1 on the bottom side), 48 nets.

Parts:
BZ1: Buzzer; CUI_CMT-5023S-SMT
C1, C2, C18, C19: 22p; C_0805
C3, C5, C11, C13: 10u; C_1206
C4, C6, C7, C8: 1u; C_0805
C9: 4.7u; C_1206
C10, C12, C15: 100n; C_0805
C14: C; C_0805
C16: 6.8n; C_0805
C17: 120n; C_0805
D1: MBRA140; DO-214AC
D2, D3, D4, D5: LED; D_0603
J1: USB_A; USB_Mini-B
J2: 1S LiPo; JST-PH2
J3: BOTTOM_HEADER; Pin_Header_Straight_1x18_Pitch2.54mm
J4: Micro_SD_Card; microSD_Card_Receptacle_Wuerth_693072010801
J5: SD_CS; Pin_Header_Straight_1x01_Pitch2.54mm
J6: TOP_HEADER; Pin_Header_Straight_1x15_Pitch2.54mm
J10, J11, J12, J13: CHASSIS_GND; MountingHole_2.7mm_M2.5_Pad
J14: 1S LiPo; Pin_Header_Straight_1x02_Pitch2.54mm
R1, R10, R11, R12, R13, R14, R15, R16: 10k; R_0805
R2, R3: 330; R_0805
R4, R5, R6: 470; R_0805
R7, R8, R9: 2k; R_0805
U1, U8: ECS-.327-12.5-17X-TR; XC1195CT-ND
U2: SPX3819M5-L-3-3; SOT-23-5
U3: ATSAMD21G18; TQFP-48_7x7mm_Pitch0.5mm
U4: MCP73831; TSOT-23-5
U5: MPL3115A2
U6: DS3231-SO16; SOIC-16W_7.5x10.3mm_Pitch1.27mm
U7: BNO055; BNO055-LGA

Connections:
+3V3: C5.1, C6.2, C8.1, C10.1, C11.1, C14.2, C16.1, C17.1, J4.4, J6.10, J6.11, R7.1, R8.1, R10.2, R11.2, R16.1, U2.5, U3.6, U3.17, U3.36, U3.44, U5.1, U5.4, U6.2, U7.3, U7.28
+BATT: C13.1, D1.2, J2.1, J6.7, J6.8, J6.9, J14.1, R12.1, U4.3
/A0: R12.2, R13.1, U3.3
/A4: J3.1, U3.10
/A5: J6.1, R2.2, U3.47
/BNO_OSC_IN: C19.1, U7.27, U8.4
/BNO_OSC_OUT: C18.1, U7.26, U8.1
/D0: J3.6, U3.16
/D1: J3.5, U3.15
/D3: J3.4, U3.14
/D4: J4.2, J5.1, U3.13
/D6: D4.2, J3.14, U3.29
/D7: D5.2, J3.15, U3.30
/D8: J3.2, U3.11
/D9: J3.3, U3.12
/D11: J3.11, U3.25
/D12: D3.2, J3.13, U3.28
/D13: J3.12, U3.26
/MISO: J3.9, J4.7, U3.21
/MOSI: J3.7, J4.3, U3.19
/OSC1: C1.1, U1.1, U3.1
/OSC2: C2.1, U1.4, U3.2
/SCK: J3.8, J4.5, U3.20
/SCL: J3.17, R7.2, U3.32, U5.8, U6.16, U7.19
/SDA: J3.16, R8.2, U3.31, U5.7, U6.15, U7.20
/SWCLK: J6.5, U3.45
/SWDIO: J6.3, U3.46
/USB_D+: J1.3, U3.34
/USB_D-: J1.2, U3.33
GND: BZ1.2, C1.2, C2.2, C3.2, C4.2, C5.2, C6.1, C7.1, C8.2, C9.2, C10.2, C11.2, C12.2, C13.2, C14.1, C15.1, C16.2, C17.2, C18.2, C19.2, J1.4, J1.5, J2.2, J3.10, J3.18, J4.6, J4.9, J6.2, J6.4, J6.6, J6.12, J6.13, J6.14, J6.15, J10.1, J11.1, J12.1, J13.1, J14.2, R4.2, R5.2, R6.2, R9.2, R13.2, R14.2, R15.1, U2.2, U3.5, U3.18, U3.35, U3.42, U4.2, U5.3, U6.13, U7.2, U7.5, U7.6, U7.15, U7.16, U7.18, U7.25
unnamed: BZ1.1, R2.1
unnamed: C4.1, U3.4
unnamed: C7.2, U3.43
unnamed: C12.1, U5.2
unnamed: C15.2, U7.9
unnamed: D2.1, R3.2
unnamed: D3.1, R4.1
unnamed: D4.1, R5.1
unnamed: D5.1, R6.1
unnamed: R1.1, U2.3
unnamed: R3.1, U4.1
unnamed: R9.1, U4.5
unnamed: R10.1, U6.1
unnamed: R11.1, U6.3
unnamed: R14.1, U7.17
unnamed: R15.2, U7.11
unnamed: R16.2, U7.4
VBUS: C3.1, C9.1, D1.1, D2.2, J1.1, R1.2, U2.1, U4.4

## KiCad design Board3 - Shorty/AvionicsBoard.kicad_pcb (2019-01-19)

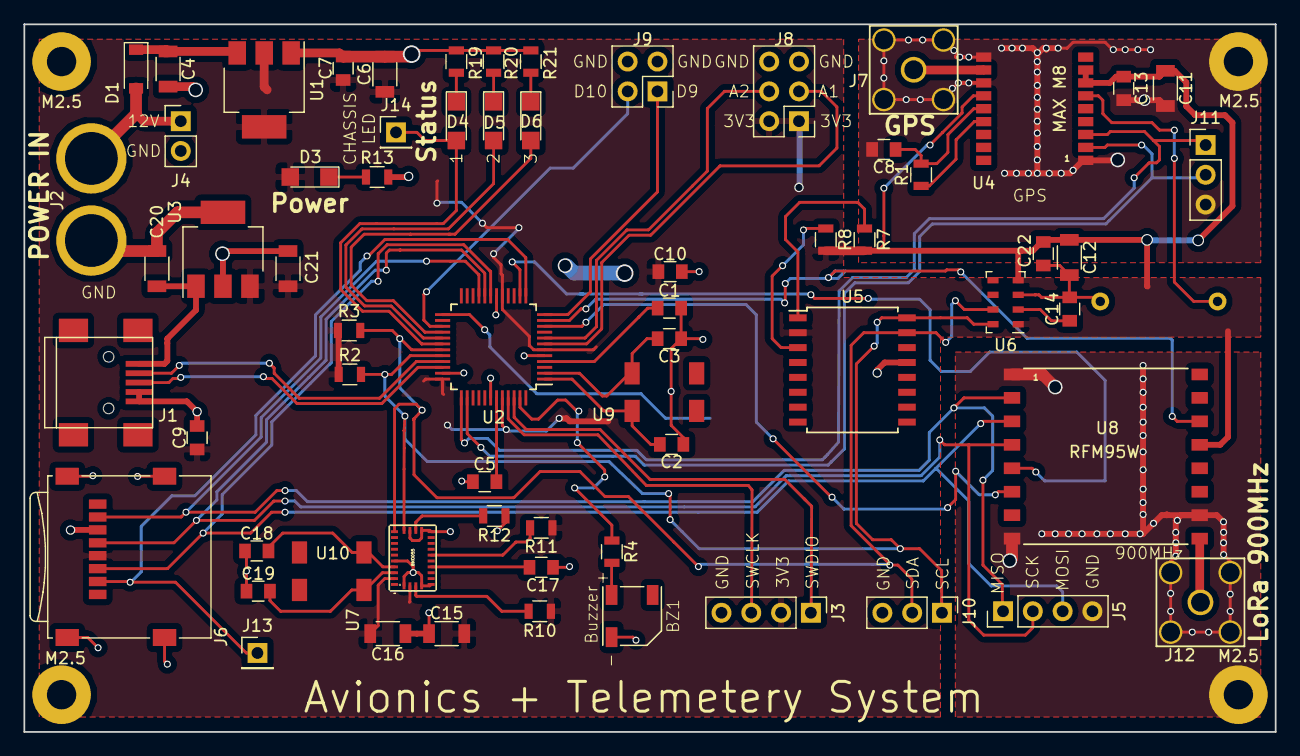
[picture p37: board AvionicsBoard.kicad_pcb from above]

Board: 2 copper layers, 106.7 x 60.3 mm, 70 parts (1 on the bottom side), 51 nets.

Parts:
BT1: Battery_Cell; BR-1225A_HB
BZ1: Buzzer; CUI_CMT-5023S-SMT
C1, C5, C9, C10: 1U; C_0805
C2, C3, C18, C19: 22p; C_0805
C4, C6, C11, C12, C20, C21: 10u; C_1206
C7, C13: 1u; C_0805
C8: 10n; C_0805
C14, C17, C22: 100n; C_0805
C15: 6.8n; C_1206
C16: 120n; C_1206
D1: D_Zener; D_SOD-123
D3, D4, D5, D6: LED; LED_1206
J1: USB_A; USB_Mini-B
J2: XT-60; XT60
J3: SWD; Pin_Header_Straight_1x04_Pitch2.54mm
J4: 12v; Pin_Header_Straight_1x02_Pitch2.54mm
J5: SPI; Pin_Header_Straight_1x04_Pitch2.54mm
J6: Micro_SD_Card; microSD_Card_Receptacle_Wuerth_693072010801
J7, J12: RF IN; SMA_TH
J8: FDBK; Pin_Header_Straight_2x03_Pitch2.54mm
J9: PWM; Pin_Header_Straight_2x02_Pitch2.54mm
J10: I2C; Pin_Header_Straight_1x03_Pitch2.54mm
J11: UART; Pin_Header_Straight_1x03_Pitch2.54mm
J13: SD_CS; Pin_Header_Straight_1x01_Pitch2.54mm
J14: CHASSIS LED; Pin_Header_Straight_1x01_Pitch2.54mm
J15, J16, J17, J18: CHASSIS GND; MountingHole_2.5mm_Pad
R1: 10; R_0805
R2, R3: 2.2k; R_0805
R4: 330; R_0805
R7, R8: 10K; R_0805
R10, R11, R12: 10k; R_0805
R13: 1k; R_0805
R19, R20, R21: 1K; R_0805
U1: LT1117CST-3.3#TRPBF; SOT-223-3_TabPin2
U2: ATSAMD21G18; TQFP-48_7x7mm_Pitch0.5mm
U3: MCP1825S; SOT-223-3_TabPin2
U4: MAX-M8W; MAX_M8
U5: DS3231-SO16; SOIC-16W_7.5x10.3mm_Pitch1.27mm
U6: MPL3115A2
U7: BNO055; BNO055-LGA
U8: RFM95W
U9, U10: ECS-.327-12.5-17X-TR; XC1195CT-ND

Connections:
+3V3: C6.1, C7.1, C9.1, C10.1, C11.1, C12.1, C13.1, C15.2, C16.2, C21.1, C22.1, D3.2, J3.2, J6.4, J8.1, J8.2, R2.1, R3.1, R7.2, R8.2, R10.1, R11.2, U1.2, U2.6, U2.17, U2.36, U2.44, U3.3, U4.7, U4.8, U4.13, U5.2, U6.1, U6.4, U7.3, U7.28, U8.13
+12V: D1.2, J2.1, J4.1
/A1: J8.3, U2.7
/A2: J8.4, U2.8
/A4: U2.10, U8.6
/A5: R4.1, U2.47
/AREF: C1.1, U2.4
/B+: BT1.1, U4.6
/D3: U2.14, U8.5
/D4: J6.2, J13.1, U2.13
/D6: D5.2, U2.29
/D7: D4.2, J14.1, U2.30
/D8: U2.11, U8.14
/D9: J9.1, U2.12
/D10: J9.2, U2.27
/D12: D6.2, U2.28
/D+: J1.3, U2.34
/D-: J1.2, U2.33
/MISO: J5.1, J6.7, U2.21, U8.2
/MOSI: J5.3, J6.3, U2.19, U8.3
/OSC1: C2.2, U2.1, U9.1
/OSC2: C3.2, U2.2, U9.4
/OSC_IN: C19.2, U7.27, U10.4
/OSC_OUT: C18.2, U7.26, U10.1
/RXD: J11.2, U2.38, U4.2
/SCK: J5.2, J6.5, U2.20, U8.4
/SCL: J10.1, R2.2, U2.32, U5.16, U6.8, U7.19
/SDA: J10.2, R3.2, U2.31, U5.15, U6.7, U7.20
/SWCLK: J3.3, U2.45
/SWDIO: J3.1, U2.46
/TXD: J11.1, U2.37, U4.3
GND: BT1.2, BZ1.2, C1.2, C2.1, C3.1, C4.2, C5.1, C6.2, C7.2, C8.2, C9.2, C10.2, C11.2, C12.2, C13.2, C14.2, C15.1, C16.1, C17.2, C18.1, C19.1, C20.2, C21.2, C22.2, J1.4, J1.5, J2.2, J3.4, J4.2, J5.4, J6.6, J6.9, J7.2, J8.5, J8.6, J9.3, J9.4, J10.3, J11.3, J12.2, J15.1, J16.1, J17.1, J18.1, R12.1, R13.2, R19.1, R20.1, R21.1, U1.1, U2.5, U2.18, U2.35, U2.42, U3.2, U4.1, U4.10, U4.12, U5.13, U6.3, U7.2, U7.5, U7.6, U7.15, U7.16, U7.18, U7.25, U8.1, U8.8, U8.10
unnamed: BZ1.1, R4.2
unnamed: C4.1, D1.1, U1.3
unnamed: C5.2, U2.43
unnamed: C8.1, R1.2, U4.14
unnamed: C14.1, U6.2
unnamed: C17.1, U7.9
unnamed: D3.1, R13.1
unnamed: D4.1, R19.2
unnamed: D5.1, R20.2
unnamed: D6.1, R21.2
unnamed: J7.1, U4.11
unnamed: J12.1, U8.9
unnamed: R1.1, U4.15
unnamed: R7.1, U5.1
unnamed: R8.1, U5.3
unnamed: R10.2, U7.4
unnamed: R11.1, U7.11
unnamed: R12.2, U7.17
VBUS: C20.1, J1.1, U3.1

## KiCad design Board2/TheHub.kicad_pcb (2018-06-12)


Board: 2 copper layers, 118.7 x 129.5 mm, 32 parts (0 on the bottom side), 25 nets.

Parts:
C1, C2, C3, C4: 10U; C_0805
D1, D2, D3, D4, D5: LED; LED_0805
J1: Actuator Fdbk Conn; Pin_Header_Straight_2x03_Pitch2.54mm
J2: Conn_01x03; Pin_Header_Straight_1x03_Pitch2.54mm
J8: 12V MAIN POWER; XT60
J11: RFD900; Socket_Strip_Angled_2x08_Pitch2.54mm
J12: I2C_1 Test Point; Pin_Header_Straight_1x03_Pitch2.54mm
J15: GPIO Test; Pin_Header_Straight_1x04_Pitch2.54mm
J17: 12V OUT; XT60
R1, R2: 220; R_0805
R3, R4: 2.2K; R_0805
R6, R7, R8: 1k; R_0805
U1: FeatherM0
U2: DS3231
U3: ArduinoNano
U4: GT-U7_GPS
U6: TL1963; SOT-223-3Lead_TabPin2
U7: LM340MP-5.0; SOT-223
U10: ADXL377
U11: BNO055
U12: MPL115A2

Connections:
+3V3: C3.1, D1.2, J1.3, J1.4, R3.1, R4.1, U1.2, U2.1, U3.15, U4.5, U6.3, U10.1, U11.1, U12.6
+5V: C4.1, D2.2, J11.4, U7.3
+12V: C1.1, C2.1, J8.1, J17.1, U6.1, U7.1
/A0: U1.5, U10.5
/A1: U1.6, U10.6
/A2: U1.7, U10.7
/A_FDBK_0: J1.1, U1.8
/A_FDBK_1: J1.2, U1.9
/ActuatorDir: J2.1, U1.24
/ActuatorPWM: J2.2, U1.23
/GPS_RX: U3.27, U4.3
/GPS_TX: U3.26, U4.2
/RFD900_RX: J11.7, U3.16
/RFD900_TX: J11.9, U3.17
/SCL_1: J12.2, R4.2, U1.18, U2.3, U11.5, U12.4
/SDA_1: J12.1, R3.2, U1.17, U2.4, U11.4, U12.3
/Status1: J15.1, R6.1, U1.19
/Status2: J15.2, R7.1, U1.21
/Status3: J15.3, R8.1, U1.22
GND: C1.2, C2.2, C3.2, C4.2, D3.1, D4.1, D5.1, J1.5, J1.6, J2.3, J8.2, J11.1, J11.2, J11.16, J12.3, J15.4, J17.2, R1.2, R2.2, U1.4, U1.16, U2.2, U3.14, U3.19, U4.4, U6.2, U7.2, U10.3, U11.3, U12.5
unnamed: D1.1, R1.1
unnamed: D2.1, R2.1
unnamed: D3.2, R6.2
unnamed: D4.2, R7.2
unnamed: D5.2, R8.2

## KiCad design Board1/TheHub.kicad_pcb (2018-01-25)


Board: 2 copper layers, 118.7 x 184.1 mm, 42 parts (0 on the bottom side), 36 nets.

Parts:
C1, C2, C3, C4: 10U; C_0805
D1, D2, D3, D4, D5, D6: LED; LED_0805
J1: Actuator Fdbk Conn; Pin_Header_Straight_2x03_Pitch2.54mm
J2: QuadEnc_Conn; Pin_Header_Straight_1x04_Pitch2.54mm
J5: NucleoLeft; NucleoSocketStrip
J8: 12V MAIN POWER; XT60
J11: RFD900; Socket_Strip_Angled_2x08_Pitch2.54mm
J12: I2C_1 Test Point; Pin_Header_Straight_1x03_Pitch2.54mm
J13: I2C_2 Test Point; Pin_Header_Straight_1x03_Pitch2.54mm
J15: GPIO Test; Pin_Header_Straight_1x04_Pitch2.54mm
J16: I2C_3 Test Point; Pin_Header_Straight_1x03_Pitch2.54mm
J17: 12V OUT; XT60
J23: NucleoRight; NucleoSocketStrip
R1, R2, R6, R7, R8, R9: 220; R_0805
R3, R4, R5, R10, R11, R12: 2.2K; R_0805
U1: Datalogger
U2: DS3231
U6: TL1963; SOT-223-3Lead_TabPin2
U7: LM340MP-5.0; SOT-223
U8: MCP9808
U10: ADXL377
U11: BNO055
U12: MPL115A2
U13: GPS; Adafruit_GPS

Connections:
+3V3: C3.1, D1.2, J1.3, J1.4, J2.1, J5.16, R3.1, R4.1, R5.1, R10.1, R11.1, R12.1, U1.7, U2.1, U6.3, U8.1, U10.1, U11.1, U12.6, U13.8
+5V: C4.1, D2.2, J5.18, J11.4, U7.3
+12V: C1.1, C2.1, J8.1, J17.1, U6.1, U7.1
/A0: J5.28, U10.5
/A1: J5.30, U10.6
/A2: J5.32, U10.7
/A_FDBK_0: J1.1, J5.36
/A_FDBK_1: J1.2, J5.38
/GPS_FIX: J23.33, U13.4
/PA2: J23.35, U13.6
/PA3: J23.37, U13.5
/PA5: J23.11, U1.5
/PA6: J15.3, J23.13, R8.1
/PA7: J15.4, J23.15, R9.1
/PA8: J16.2, J23.23, R12.2
/PA11: J11.7, J23.14
/PA12: J11.9, J23.12
/PB3: J13.1, J23.31, R5.2
/PB4: J23.27, U1.3
/PB5: J23.29, U1.4
/PB6: J12.2, J23.17, R4.2, U2.3, U8.3, U11.5, U12.4
/PB7: J5.21, J12.1, R3.2, U2.4, U8.4, U11.4, U12.3
/PB10: J13.2, J23.25, R10.2
/PB13: J2.3, J23.30
/PB14: J2.2, J23.28
/PC4: J15.1, J23.34, R6.1
/PC5: J15.2, J23.6, R7.1
/PC9: J16.1, J23.1, R11.2
/PD2: J5.4, U1.2
GND: C1.2, C2.2, C3.2, C4.2, D3.1, D4.1, D5.1, D6.1, J1.5, J1.6, J2.4, J5.8, J5.19, J5.20, J5.22, J8.2, J11.1, J11.2, J11.16, J12.3, J13.3, J16.3, J17.2, J23.9, J23.20, R1.2, R2.2, U1.6, U2.2, U6.2, U7.2, U8.2, U10.3, U11.3, U12.5, U13.7
unnamed: D1.1, R1.1
unnamed: D2.1, R2.1
unnamed: D3.2, R6.2
unnamed: D4.2, R7.2
unnamed: D5.2, R8.2
unnamed: D6.2, R9.2

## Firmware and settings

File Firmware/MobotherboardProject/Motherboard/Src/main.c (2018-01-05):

/**
  ******************************************************************************
  * File Name          : main.c
  * Description        : Main program body
  ******************************************************************************
  *
  * COPYRIGHT(c) 2017 STMicroelectronics
  *
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
  ******************************************************************************
  */
/* Includes ------------------------------------------------------------------*/
#include "main.h"
#include "stm32f4xx_hal.h"

I2C_HandleTypeDef hi2c1;
I2C_HandleTypeDef hi2c2;

UART_HandleTypeDef huart1;
UART_HandleTypeDef huart6;

/* USER CODE BEGIN PV */

/* USER CODE END PV */

void write_8bit_register(uint8_t register_pointer, uint16_t register_value);
void write_16bit_register(uint8_t register_pointer, uint16_t register_value);
void pca9685_init(I2C_HandleTypeDef *hi2c, uint8_t address);
void pca9685_pwm(I2C_HandleTypeDef *hi2c, uint8_t address, uint8_t num, uint16_t on, uint16_t off);
void SystemClock_Config(void);
void Error_Handler(void);
static void MX_GPIO_Init(void);
static void MX_I2C2_Init(void);
static void MX_USART6_UART_Init(void);
static void MX_USART1_UART_Init(void);
static void MX_I2C1_Init(void);

/* USER CODE BEGIN PFP */

/* USER CODE END PFP */

int main(void)
{

  /* MCU Configuration----------------------------------------------------------*/

  /* Reset of all peripherals, Initializes the Flash interface and the Systick. */
  HAL_Init();

  /* Configure the system clock */
  SystemClock_Config();

  /* Initialize all configured peripherals */
  MX_GPIO_Init();
  MX_I2C2_Init();
  MX_USART6_UART_Init();
  MX_USART1_UART_Init();
  MX_I2C1_Init();

  /* USER CODE BEGIN 2 */
  uint8_t Test[] = "Hello World!";
  uint8_t Packet[17];
  uint8_t PWMPacket[50];
  PWMPacket[0] = 0x12;
  PWMPacket[1] = 0x21;
  PWMPacket[2] = 0x45;
  /* USER CODE END 2 */

  /* Infinite loop */
  /* USER CODE BEGIN WHILE */

  write_8bit_register(0x0, 0x0);	//reset PCA9685

  while (1)
  {
	  HAL_UART_Receive(&huart6,Packet,sizeof(Packet),10);
	  //HAL_Delay(20);
	  HAL_UART_Transmit(&huart6,Test,sizeof(Test), 10);
	  HAL_Delay(1);
//	  for(int i=0; i<3; i++){
//		 // HAL_I2C_Master_Transmit(&hi2c1,0x40<<1,PWMPacket[i],sizeof(PWMPacket[i]),10);
//		  HAL_I2C_Master_Transmit(&hi2c1, 0x80, &PWMPacket[i], 1, 1);
//		  //HAL_Delay(0.00001);
//	  }
	  //raw packet -> clean packet by verifying <[size of packet]> or some other checksum library
	  //HAL_GPIO_TogglePin(GPIOA, GPIO_PIN_6);
	  //HAL_Delay(1);
  /* USER CODE END WHILE */
	  pca9685_init(&hi2c1, 0x80);
	  write_8bit_register(0xFE, 0x03);		//set frequency of clock to 200HZ
//	  write_16bit_register(0x42, 500);
//	  write_16bit_register(0x44, 1000);
//	  HAL_Delay(50);
//  /* USER CODE BEGIN 3 */
	   pca9685_pwm(&hi2c1, 0x80, 15, 0, 1024);
	   HAL_Delay(5);



  }
  /* USER CODE END 3 */

}

//void PCA9685_setPrescale(uint8_t prescale){
//	uint8_t oldmode =
//}

void write_8bit_register(uint8_t register_pointer, uint16_t register_value){
    uint8_t data[3];

    data[0] = register_pointer;     // register address
    data[1] = register_value;       // byte of data

    HAL_I2C_Master_Transmit(&hi2c1, 0x40<<1, data, 2, 100);  // data is the start pointer of our array
}

void write_16bit_register(uint8_t register_pointer, uint16_t register_value){
    uint8_t data[3];

    data[0] = register_pointer;     // 0x0C in your example
    data[1] = register_value>>8;    // MSB byte of 16bit data
    data[2] = register_value;       // LSB byte of 16bit data

    HAL_I2C_Master_Transmit(&hi2c1, 0x40<<1, data, 3, 100);  // data is the start pointer of our array
}

void pca9685_init(I2C_HandleTypeDef *hi2c, uint8_t address){
 #define PCA9685_MODE1 0x00
 uint8_t initStruct[2];
 uint8_t prescale = 3; // hardcoded
 HAL_I2C_Master_Transmit(hi2c, address, 0x00, 1, 1);
 uint8_t oldmode = 0; // hardcoded
 // HAL_I2C_Master_Receive(hi2c, address, &oldmode, 1, 1);
 uint8_t newmode = ((oldmode & 0x7F) | 0x10);
 initStruct[0] = PCA9685_MODE1;
 initStruct[1] = newmode;
 HAL_I2C_Master_Transmit(hi2c, address, initStruct, 2, 1);
 initStruct[1] = prescale;
 HAL_I2C_Master_Transmit(hi2c, address, initStruct, 2, 1);
 initStruct[1] = oldmode;
 HAL_I2C_Master_Transmit(hi2c, address, initStruct, 2, 1);
 HAL_Delay(5);
 initStruct[1] = (oldmode | 0xA1);
 HAL_I2C_Master_Transmit(hi2c, address, initStruct, 2, 1);
}

void pca9685_pwm(I2C_HandleTypeDef *hi2c, uint8_t address, uint8_t num, uint16_t on, uint16_t off){
 uint8_t outputBuffer[5] = {0x06 + 4*num, on, (on >> 8), off, (off >> 8)};
 HAL_I2C_Master_Transmit(&hi2c1, address, outputBuffer, 5, 1);
}

/** System Clock Configuration
*/
void SystemClock_Config(void)
{

  RCC_OscInitTypeDef RCC_OscInitStruct;
  RCC_ClkInitTypeDef RCC_ClkInitStruct;

    /**Configure the main internal regulator output voltage 
    */
  __HAL_RCC_PWR_CLK_ENABLE();

  __HAL_PWR_VOLTAGESCALING_CONFIG(PWR_REGULATOR_VOLTAGE_SCALE1);

    /**Initializes the CPU, AHB and APB busses clocks 
    */
  RCC_OscInitStruct.OscillatorType = RCC_OSCILLATORTYPE_HSI;
  RCC_OscInitStruct.HSIState = RCC_HSI_ON;
  RCC_OscInitStruct.HSICalibrationValue = 16;
  RCC_OscInitStruct.PLL.PLLState = RCC_PLL_ON;
  RCC_OscInitStruct.PLL.PLLSource = RCC_PLLSOURCE_HSI;
  RCC_OscInitStruct.PLL.PLLM = 8;
  RCC_OscInitStruct.PLL.PLLN = 100;
  RCC_OscInitStruct.PLL.PLLP = RCC_PLLP_DIV2;
  RCC_OscInitStruct.PLL.PLLQ = 4;
  if (HAL_RCC_OscConfig(&RCC_OscInitStruct) != HAL_OK)
  {
    Error_Handler();
  }

    /**Initializes the CPU, AHB and APB busses clocks 
    */
  RCC_ClkInitStruct.ClockType = RCC_CLOCKTYPE_HCLK|RCC_CLOCKTYPE_SYSCLK
                              |RCC_CLOCKTYPE_PCLK1|RCC_CLOCKTYPE_PCLK2;
  RCC_ClkInitStruct.SYSCLKSource = RCC_SYSCLKSOURCE_PLLCLK;
  RCC_ClkInitStruct.AHBCLKDivider = RCC_SYSCLK_DIV1;
  RCC_ClkInitStruct.APB1CLKDivider = RCC_HCLK_DIV4;
  RCC_ClkInitStruct.APB2CLKDivider = RCC_HCLK_DIV1;

  if (HAL_RCC_ClockConfig(&RCC_ClkInitStruct, FLASH_LATENCY_3) != HAL_OK)
  {
    Error_Handler();
  }

    /**Configure the Systick interrupt time 
    */
  HAL_SYSTICK_Config(HAL_RCC_GetHCLKFreq()/1000);

    /**Configure the Systick 
    */
  HAL_SYSTICK_CLKSourceConfig(SYSTICK_CLKSOURCE_HCLK);

  /* SysTick_IRQn interrupt configuration */
  HAL_NVIC_SetPriority(SysTick_IRQn, 0, 0);
}

/* I2C1 init function */
static void MX_I2C1_Init(void)
{

  hi2c1.Instance = I2C1;
  hi2c1.Init.ClockSpeed = 100000;
  hi2c1.Init.DutyCycle = I2C_DUTYCYCLE_2;
  hi2c1.Init.OwnAddress1 = 0;
  hi2c1.Init.AddressingMode = I2C_ADDRESSINGMODE_7BIT;
  hi2c1.Init.DualAddressMode = I2C_DUALADDRESS_DISABLE;
  hi2c1.Init.OwnAddress2 = 0;
  hi2c1.Init.GeneralCallMode = I2C_GENERALCALL_DISABLE;
  hi2c1.Init.NoStretchMode = I2C_NOSTRETCH_DISABLE;
  if (HAL_I2C_Init(&hi2c1) != HAL_OK)
  {
    Error_Handler();
  }

}

/* I2C2 init function */
static void MX_I2C2_Init(void)
{

  hi2c2.Instance = I2C2;
  hi2c2.Init.ClockSpeed = 100000;
  hi2c2.Init.DutyCycle = I2C_DUTYCYCLE_2;
  hi2c2.Init.OwnAddress1 = 0;
  hi2c2.Init.AddressingMode = I2C_ADDRESSINGMODE_7BIT;
  hi2c2.Init.DualAddressMode = I2C_DUALADDRESS_DISABLE;
  hi2c2.Init.OwnAddress2 = 0;
  hi2c2.Init.GeneralCallMode = I2C_GENERALCALL_DISABLE;
  hi2c2.Init.NoStretchMode = I2C_NOSTRETCH_DISABLE;
  if (HAL_I2C_Init(&hi2c2) != HAL_OK)
  {
    Error_Handler();
  }

}

/* USART1 init function */
static void MX_USART1_UART_Init(void)
{

  huart1.Instance = USART1;
  huart1.Init.BaudRate = 9600;
  huart1.Init.WordLength = UART_WORDLENGTH_8B;
  huart1.Init.StopBits = UART_STOPBITS_1;
  huart1.Init.Parity = UART_PARITY_NONE;
  huart1.Init.Mode = UART_MODE_TX_RX;
  huart1.Init.HwFlowCtl = UART_HWCONTROL_NONE;
  huart1.Init.OverSampling = UART_OVERSAMPLING_16;
  if (HAL_UART_Init(&huart1) != HAL_OK)
  {
    Error_Handler();
  }

}

/* USART6 init function */
static void MX_USART6_UART_Init(void)
{

  huart6.Instance = USART6;
  huart6.Init.BaudRate = 9600;
  huart6.Init.WordLength = UART_WORDLENGTH_8B;
  huart6.Init.StopBits = UART_STOPBITS_1;
  huart6.Init.Parity = UART_PARITY_NONE;
  huart6.Init.Mode = UART_MODE_TX_RX;
  huart6.Init.HwFlowCtl = UART_HWCONTROL_NONE;
  huart6.Init.OverSampling = UART_OVERSAMPLING_16;
  if (HAL_UART_Init(&huart6) != HAL_OK)
  {
    Error_Handler();
  }

}

/** Configure pins as 
        * Analog 
        * Input 
        * Output
        * EVENT_OUT
        * EXTI
*/
static void MX_GPIO_Init(void)
{

  GPIO_InitTypeDef GPIO_InitStruct;

  /* GPIO Ports Clock Enable */
  __HAL_RCC_GPIOC_CLK_ENABLE();
  __HAL_RCC_GPIOH_CLK_ENABLE();
  __HAL_RCC_GPIOA_CLK_ENABLE();
  __HAL_RCC_GPIOB_CLK_ENABLE();

  /*Configure GPIO pin Output Level */
  HAL_GPIO_WritePin(GPIOA, GPIO_PIN_6|GPIO_PIN_7, GPIO_PIN_RESET);

  /*Configure GPIO pin Output Level */
  HAL_GPIO_WritePin(GPIOC, GPIO_PIN_4|GPIO_PIN_5, GPIO_PIN_RESET);

  /*Configure GPIO pin : PC13 */
  GPIO_InitStruct.Pin = GPIO_PIN_13;
  GPIO_InitStruct.Mode = GPIO_MODE_INPUT;
  GPIO_InitStruct.Pull = GPIO_PULLDOWN;
  HAL_GPIO_Init(GPIOC, &GPIO_InitStruct);

  /*Configure GPIO pins : PA6 PA7 */
  GPIO_InitStruct.Pin = GPIO_PIN_6|GPIO_PIN_7;
  GPIO_InitStruct.Mode = GPIO_MODE_OUTPUT_PP;
  GPIO_InitStruct.Pull = GPIO_NOPULL;
  GPIO_InitStruct.Speed = GPIO_SPEED_FREQ_LOW;
  HAL_GPIO_Init(GPIOA, &GPIO_InitStruct);

  /*Configure GPIO pins : PC4 PC5 */
  GPIO_InitStruct.Pin = GPIO_PIN_4|GPIO_PIN_5;
  GPIO_InitStruct.Mode = GPIO_MODE_OUTPUT_PP;
  GPIO_InitStruct.Pull = GPIO_NOPULL;
  GPIO_InitStruct.Speed = GPIO_SPEED_FREQ_LOW;
  HAL_GPIO_Init(GPIOC, &GPIO_InitStruct);

}

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


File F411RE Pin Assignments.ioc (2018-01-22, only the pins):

Mcu.UserName=STM32F411RETx
PA0-WKUP.Signal=ADCx_IN0
PA1.Signal=ADCx_IN1
PA10.Signal=GPIO_Input
PA11.Signal=USART6_TX
PA12.Signal=USART6_RX
PA2.Signal=USART2_TX
PA3.Signal=USART2_RX
PA4.Signal=ADCx_IN4
PA5.Signal=SPI1_SCK
PA6.Signal=S_TIM3_CH1
PA7.Signal=S_TIM3_CH2
PA8.Signal=I2C3_SCL
PB10.Signal=I2C2_SCL
PB13.GPIO_Label=Quad Encoder ChA
PB13.Signal=GPIO_Input
PB14.GPIO_Label=Quad Encoder ChB
PB14.Signal=GPIO_Input
PB3.Signal=I2C2_SDA
PB4.Signal=SPI1_MISO
PB5.Signal=SPI1_MOSI
PB6.Signal=I2C1_SCL
PB7.Signal=I2C1_SDA
PC0.Signal=ADCx_IN10
PC1.Signal=ADCx_IN11
PC9.Signal=I2C3_SDA
PD2.GPIO_Label=ChipSelect SD
PD2.Signal=GPIO_Output

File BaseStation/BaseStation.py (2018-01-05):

__author__ = 'Danny'

import time
import pygame
import serial

pygame.init()
pygame.joystick.init()
done = False
counter = 0
lastButton = 0

joystickWheels = pygame.joystick.Joystick(0)
joystickWheels.init()
joystickArm = pygame.joystick.Joystick(0)
joystickArm.init()


def getJoyVal(joystick, axis, deadband):
    # type: (object, object) -> object
    "this function returns the value of a joystick, given an axis and a joystick number"
    if abs(joystick.get_axis(axis)) > deadband:
        Value = 255 - (int(round(127 * joystick.get_axis(axis))) + 127)
    else:
        Value = 127
    # map (-1 to 1) to (0.10 to 0.20) for PWM
    # pwm = chr(Value)
    # fpwm = '{:4.4}'.format(pwm)     #for sending direct pwm value
    return Value


def getHat(axis, joystick, number):
    if axis == 'x':
        if str(joystick.get_hat(number))[1] == '1':
            value = 64
        elif str(joystick.get_hat(number))[1] == '-':
            value = 192
        else:
            value = 127
    if axis == 'y':
        if str(joystick.get_hat(number))[4] == '1':
            value = 192
        elif str(joystick.get_hat(number))[4] == '-':
            value = 64
        else:
            value = 127
    return value


def getState(button):
    global counter
    global lastButton
    if (button == 1) and (lastButton == 0):
        lastButton = 1
        state = counter
        counter += 1
        if counter >= 3:
            counter = 0
        return state
    if button == 0:
        lastButton = 0


ser = serial.Serial('COM4', 9600)  # open first serial port
# print ser.portstr       # check which port was really used
# ser.write("<@@@>")      # write a string
# ser.close()





while 1:
    pygame.event.get()
    my_bytes = bytearray()

    # if(joystickArm.get_button(1)):
    #     armActuator

    # if getState == 0:
    my_bytes.append(60)
    my_bytes.append(getJoyVal(joystickWheels, 1, 0.05))  # 1 left wheels
    my_bytes.append(getJoyVal(joystickWheels, 3, 0.05))  # 2 right wheels
    my_bytes.append(getHat('x', joystickWheels, 0))  # 3 cam pan, wheels hat
    my_bytes.append(getHat('y', joystickWheels, 0))  # 4 cam tilt, wheels hat
    if (joystickWheels.get_button(7) == 1):
        my_bytes.append(64)  # 5 cam select, select button
    if (joystickWheels.get_button(7) == 0):
        my_bytes.append(192)  # 5 cam select, select button
    ###########Arm Actuators##########
    if joystickArm.get_button(0) == 1:
        my_bytes.append(getJoyVal(joystickArm, 1, 0.05))  # 6 upper arm speed - axis 3
        my_bytes.append(127)  # 7 lower arm speed
    if joystickArm.get_button(0) == 0:
        my_bytes.append(127)  # 6 upper arm speed - axis 3
        my_bytes.append(255 - getJoyVal(joystickArm, 1, 0.05))  # 7 lower arm speed
    ##################################
    ##########Base Rotation###########
    my_bytes.append(255 - getJoyVal(joystickArm, 0, 0.15))  # 8 base rotation
    ##################################
    ##########Wrist Rotation##########
    if joystickArm.get_button(4) == 1:
        my_bytes.append(30)  # 9 wrist rot - x and y
    elif joystickArm.get_button(5) == 1:
        my_bytes.append(220)
    else:
        my_bytes.append(127)  # 9 wrist rot - x and y
    my_bytes.append(255 - getJoyVal(joystickArm, 4, 0.15))  # 10 wrist yaw - axis 4?
    #################################
    ##########Wrist Pitch###########
    # if(getJoyVal(joystickArm, 3, 0.15) < 45):
    #     my_bytes.append(45)
    # if(getJoyVal(joystickArm, 3, 0.15) >= 170):
    #     my_bytes.append(85)
    # else:
    #     my_bytes.append(255-getJoyVal(joystickArm, 3, 0.05))  # 11 wrist pitch - axis 1
    my_bytes.append(getHat('y', joystickArm, 0))  # 11 wrist pitch - arm hat y
    ###############################
    my_bytes.append(getJoyVal(joystickArm, 2, 0.15))  # 12 wrist claw - axis 2?
    if (joystickArm.get_button(6) == 1):
        my_bytes.append(115)  # 13 soil sensor request
    else:
        my_bytes.append(127)
    my_bytes.append(127)  # 14 gps request
    my_bytes.append(62)

    # bytesToRead = ser.inWaiting()
    # print ser.read(bytesToRead)

    # z = '<'+chr(y1)+chr(y2)+'a'+'>'
    # z = bytes(0x3c)+bytes(0x40)+bytes(0x56)+bytes(0x55)+bytes(0x3E)
    # z=[float(x1),float(y1),float(x2),float(y2)]

    # ser.write(str(z))
    # print getHat('y',joystickWheels,0)
    print(my_bytes)

    ser.write(my_bytes)
    # bytesToRead = ser.inWaiting()
    # print ser.read(bytesToRead)
    time.sleep(.05)

    # ser.close()

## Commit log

2018-01-05 Copy work from "The Hub"
    The Hub is a board that is used for quickly prototyping and testing software meant for the final board revision. It is easier to make modifications to and has a higher success rate than custom PCBs.
    [Motherboard.cfg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]
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2018-01-06 Add pin assignments for 2xPWM, I2C 1-3, UART2, UART6, and ADC 0-2
    Pin assignments can be viewed in STMCube MX from the .ioc file
    [_saved_TheHub.sch]
2018-01-07 Add note or BNO055, add GPS, add nucleo pin declaration for GPS_FIX GPIO_Input
    [TheHub.sch, _saved_TheHub.sch]
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2018-01-08 Add MPL115A2 footprint, annotate schematic
    [TheHub.sch]
2018-01-08 Associate parts using CvPCB
    [TheHub.sch]
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2018-01-08 Make PCB have smaller profile
    [TheHub.kicad_pcb]
2018-01-08 Created center line and aligned gyro and accelerometers
    [TheHub.kicad_pcb]
2018-01-08 Route all signal and power traces
    [TheHub.kicad_pcb]
2018-01-08 Add offset to 3D model on nucleo pins so that they display correctly
    [TheHub.kicad_pcb]
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2018-01-08 Add logo to the board
    [TheHub.kicad_pcb]
2018-01-08 Add labeling text for probe points
    [TheHub-B.Cu.gbl, TheHub-B.Mask.gbs, TheHub-B.SilkS.gbo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]
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2018-01-10 Update XT60 connectors, replae old XT60 footprint on board, generate new gerbers
    [TheHub-B.Cu.gbl, TheHub-B.Mask.gbs, TheHub-B.SilkS.gbo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]
2018-01-10 Update MPL115A2 on pcb to current footprint
    [TheHub.kicad_pcb]
2018-01-11 Add mounting points for RFD900
    [TheHub.kicad_pcb]
2018-01-22 Add to schematic and CubeMX: IO for SD card datalogger, 2x analog pot inputs, quad encoder
    [TheHub.sch]
2018-01-22 Add Datalogger library schematic and integrate into schematic
    [TheHub.sch]
2018-01-22 Eat dinner, create footprint for Datalogger
    [_saved_TheHub.sch]
2018-01-22 Add DS3231 to schematic lib, integrate DS3231 into schematic
    [TheHub.sch, _saved_TheHub.sch]
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2018-01-22 Associate schematic with footprints
    [TheHub.sch]
2018-01-22 Update netlist to use staight headars instead of angled
    [TheHub.sch]
2018-01-22 Add Datalogger and RTC to PCB, add I2C addresses to silkscreen
    [TheHub.kicad_pcb]
2018-01-22 Add silkscreen lables for RX, TX, Nucleo, and analog feedback
    [TheHub.kicad_pcb]
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2018-04-19 Create new schematic for Feather M0
    Copied form th Nucleo Hub, add Nano and Feather M0 schematics
    [TheHub-B.Cu.gbl, TheHub-B.Mask.gbs, TheHub-B.SilkS.gbo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]
2018-04-19 Create footprint for Feather M0, correct schematic changes
    [TheHub.sch]
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2018-04-19 Remove previous components from the board
    [TheHub.kicad_pcb]
2018-04-19 Relayout Hub 2 Board
    [TheHub.kicad_pcb, TheHub.sch]
2018-04-19 Add nice text markings
    [TheHub.kicad_pcb]
2018-04-20 Modify RFD footprint, generate Gerbs
    [TheHub-B.Cu.gbl, TheHub-B.Mask.gbs, TheHub-B.SilkS.gbo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]
2018-06-12 Add most of the schematic fo the new board
    [AvionicsBoard.kicad_pcb, AvionicsBoard.sch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]
2018-06-12 Associate some arts, make some schematic changes
    [AvionicsBoard.sch]
2018-06-13 create more footprints, associate parts
    [_saved_AvionicsBoard.sch]
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2018-06-17 Finished routing board, added logo
    [AvionicsBoard.kicad_pcb, AvionicsBoard.sch]
2018-07-04 Fix BNO055 footprint and board layout
    [2018-06-23T18_30_49.csv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]
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2018-10-31 Change CS for SD card to PA08 (aka pin 13), Add RDF900 Serial ports, Add 0 ohm GPS selectors, add GT-07 GPS, add 5v regualtor for RFD900
    [AvionicsBoard.kicad_pcb, AvionicsBoard.sch, _saved_TheHub.sch]
2018-11-01 Little bit o PCB layout
    [AvionicsBoard.kicad_pcb]
2018-11-02 Get that RFD900 UART outta the uC to that radio
    [AvionicsBoard.kicad_pcb, _saved_TheHub.sch]
2018-11-03 Make board that is too fat
    [AvionicsBoard.kicad_pcb]
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2018-11-03 Add LEDs, cleanup traces
    [AvionicsBoard.kicad_pcb, AvionicsBoard.sch, _saved_AvionicsBoard.sch]
2018-11-03 Added finshing touches to board. Investigate GPS and RFM95 RF paths!! RFD900 mounting hole sneed resizing!!
    [AvionicsBoard.kicad_pcb, RFD900X.stp, _saved_AvionicsBoard.sch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]
2018-11-03 Add solidworks chassis
    cleanup folders later
    [132170_3d_model_file.SLDASM, 3318.SLDPRT, 3318.STEP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]
2018-11-03 Add Avionics Cost Document
    [Avionics Cost.xlsx]
2018-12-10 Finishing touches on RF
    [AvionicsBoard.kicad_pcb]
2018-12-10 Do some board cleanup, generate gerbs
    [AvionicsBoard-B.Cu.gbl, AvionicsBoard-B.Mask.gbs, AvionicsBoard-B.SilkS.gbo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]
2019-01-06 Add buzzer, LorA interrupt and reset lines, fix issue with USB and battery power, reduce RF path lengths, add better microstrip matching for LoRa and GPS, create ALLPCB BOM
    [AvionicsBoard.kicad_pcb, AvionicsBoard.sch, Board3 BOM.xlsx]
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2019-01-06 Update cost option 4
    [AvionicsBoard.kicad_pcb, Board3 BOM.xlsx]
2019-01-06 Add Cyclone Rocketry Logo, generate gerbers
    [AvionicsBoard-B.Cu.gbl, AvionicsBoard-B.Mask.gbs, AvionicsBoard-B.SilkS.gbo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]
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2019-03-24 Connect JST connector to VBatt+ and GND nets
    [18650 Holder.SLDPRT, 18650 Li-Ion.SLDPRT, Avionics Board 1-2019-03-23-16-37-36.sch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]
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2019-04-03 Remove DS3231 and expand the J3 connector to include USB and improve pin ordering. Various bug fixes
    [Avionics Board 1.kicad_pcb, Avionics Board 1.sch]
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2019-04-08 Create the Hub 2, a smaller version of the original hub that will fit inside a rocket
    [AvionicsBoard-2019-04-04-00-17-48.sch, TheHub-2019-04-07-21-51-38.sch, TheHub2.kicad_pcb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]
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2019-04-09 For Hub2: add servo2 and GPS changed to breakout for MAX M8Q
    [TheHub2-B_Cu.gbl, TheHub2-B_Mask.gbs, TheHub2-B_SilkS.gbo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]
2019-05-01 Add micro SD Card, clean up ref des, power 6v boost directly from battery instead of 3.3V rail
    [Avionics Board 1.kicad_pcb, Avionics Board 1.sch, _saved_Avionics Board 1.sch]
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2019-05-01 Create Gerbers, move SD card up for more error margin
    [Avionics Board 1-B_Cu.gbr, Avionics Board 1-B_Mask.gbr, Avionics Board 1-B_SilkS.gbr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]

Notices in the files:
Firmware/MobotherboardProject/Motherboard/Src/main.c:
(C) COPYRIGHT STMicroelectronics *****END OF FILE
